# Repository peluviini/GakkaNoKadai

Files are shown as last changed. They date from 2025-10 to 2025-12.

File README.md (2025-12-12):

## GAS + Arduino kinda IOT Project
I'm making automatic controled fan that turns towards the hottest direction(assuming Human).

The fun's speeed is adjusted by caluculated Appearannce Temperature.

You can set some parameters in webpage, like targeted temperature, periodical notifications in discord.

> this is some practical assignment of my department 

### gas

Using clasp and so typescript

Gas is launching html

To deploy and see the page
> sh deploy.sh

### arduino
Trying to use esp-idf of rust

generate project->
> cargo generate esp-rs/esp-idf-template cargo

### memoranda
[GoogleSheet](https://docs.google.com/spreadsheets/d/12KPpMY7eV-cPQyw1QVUG0R_QObp-cpFYQhn_H8V2V_I/edit?gid=0#gid=0)

[See GAS codes](https://script.google.com/home/projects/1Yt5xZ93DhFCQdzscJVXwyot8o_8Z_F5k2Kss0VgZLZjdxhrT6P_gblSO/edit)

Page -> `sh deploy.sh` on gas directry

↓レポートのコピペ

<br>

# 1, 目的
### 電子デバイスを試行錯誤して作製する経験により,主体的に電子デバイス開発を行う能力をみにつける.

<br>

# 2, 原理・基礎的知見
## 2.1, 使用したセンサの概略と動作原理
## 2.1.1, 赤外線アレイセンサー
### 視野角60度の範囲を8×8ピクセルに分割して温度を取得する赤外線センサー.

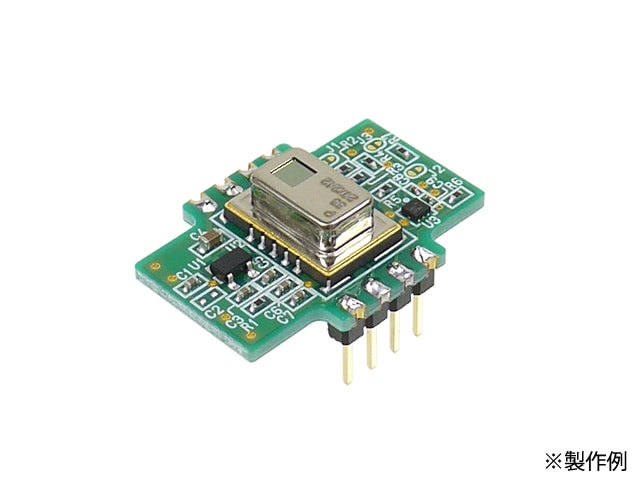
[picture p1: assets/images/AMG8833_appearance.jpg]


[AMG8833使用 赤外線アレイセンサー(Grid-EYE)モジュール](https://akizukidenshi.com/catalog/g/g116737/)

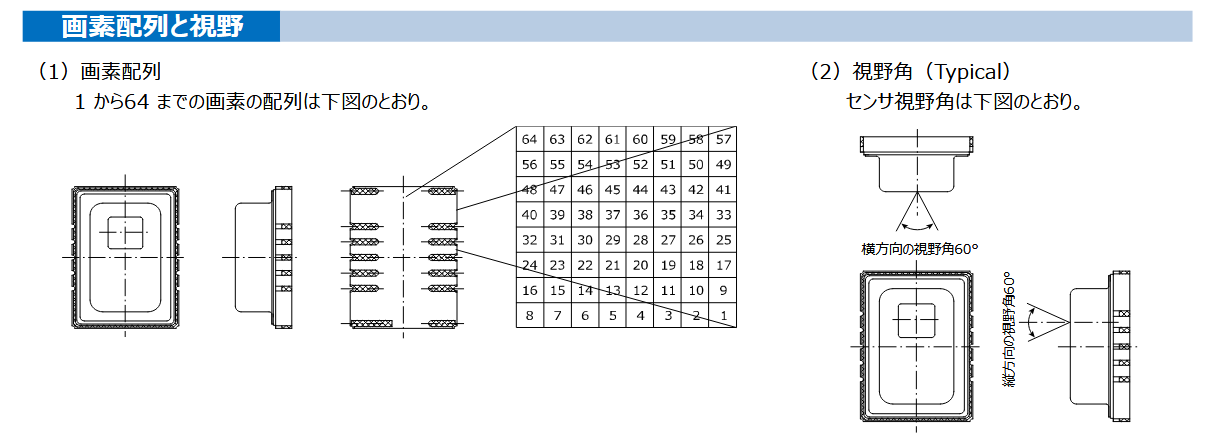
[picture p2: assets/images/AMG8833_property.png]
特性:画素配列と視野角


### 使用概略としては,値を縦方向に分割し方向ごとの合計値を計算,比較して熱の集まる方向として角度(ラジアン値)を判定する.

<br>

## 2.1.1, 温湿度センサー
### 温度及び湿度を取得するセンサー.

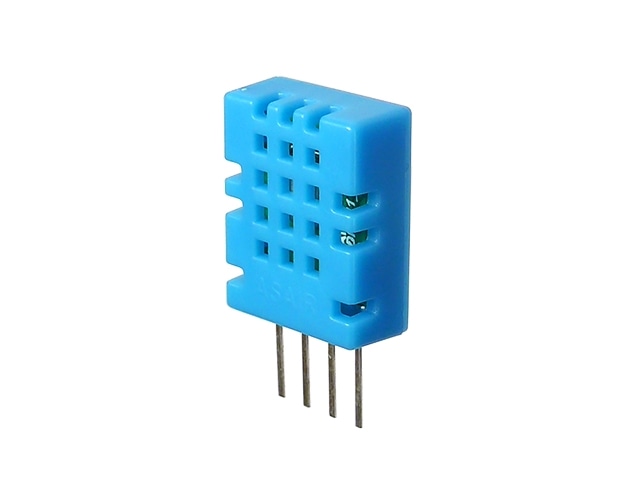
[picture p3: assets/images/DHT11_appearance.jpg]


[温湿度センサー モジュール DHT11](https://akizukidenshi.com/catalog/g/g107003/)

<br>

## 2.2, そのほか, 使用した特徴的な素子の概略と動作原理
## 2.2.1, USB PD シンクコントローラー
### type-c dip化モジュールと併せて使用し,PD規格とその給電する電力をコントロールするic. 今回のプロジェクトでは9[V]電源を得るために使用した.
[USB PD+BC シンクコントローラー CH224K](https://akizukidenshi.com/catalog/g/g118023/)

## 2.2.2, 三端子DCDCレギュレーター 5V
### 任意の電圧を5[V]に降圧する素子. esp-32などへの給電に使用.
[三端子DCDCレギュレーター 5V BP5293-50](https://akizukidenshi.com/catalog/g/g111188/)

<br>

# 3, 作品制作の実施概要
## 3.1, 作品名・キャッチコピー
### 作品名 「オートファ-トン」
### 全てが自律して動く卓上扇風機.

## 3.2, 制作の背景・目的
### デスクワークなどの作業では,常に同じ姿勢を保ち続けることは少なく,体の向きや位置は無意識のうちに変化する. 特に夏場,扇風機の風から体が外れてしまうもどかしさを経験した人は多いだろう. 従来の据え置き型扇風機は,一方向への送風や首振り機能によって一定範囲をカバーできるものの,それ以上の複雑な動きには対応できず,小回りが利かない.
### そこで今プロジェクトでは,使用者を自律的に追従し,常に適切な位置へ風を送り続け,さらに風量調節などの操作も自動化した卓上扇風機を開発する.

## 3.3, 想定ユーザーと利用シーン
### デスクワークをする人. 夏場ないし気温の高い日の屋内. その他, 対象が動く可能性があるが常に冷やし続けなければいけない状況.

## 3.4, 機能の概要
+ ### 人の体を検知/追尾し,風を常に当て続けてくれる
+ ### 温度と湿度,設定したターゲット体感温度から風量を自動で調節
### の2機能を備え,デバイス設定やリモコンとしての操作はすべてwebブラウザで行うことができる.
### また,部屋の温度をwebブラウザから確認することができる.

<br>

## 3.5, 構成要素と仕組み
## 3.5.1, 使用部品・物品
### 本体
+ ### ファン : Noctua NF-A20 5V PWM [商品ページ](https://www.google.com/url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)
+ ### モーター : FEETECHサーボ FT5325M [商品ページ](https://akizukidenshi.com/catalog/g/g116310/)
+ ### マイコン : ESP32-32D N4 [製品ページ](https://www.digikey.jp/ja/products/detail/espressif-systems/ESP32-WROOM-32D-N4/9381716)
+ ### 温湿度センサー モジュール DHT11　[商品ページ](https://akizukidenshi.com/catalog/g/g107003/)
+ ### USBtype-CコネクターDIP化キット [商品ページ](https://akizukidenshi.com/catalog/g/g115426/)
+ ### USB PD シンクコントローラー CH221K　[商品ページ](https://akizukidenshi.com/catalog/g/g118022/)
+ ### 三端子DCDCレギュレーター 5V BP5293-50 [商品ページ](https://akizukidenshi.com/catalog/g/g111188/)
+ ### LM2596 DC - DC降圧コンバータモジュール [商品ページ](https://www.amazon.co.jp/%E3%83%95%E3%83%AA%E3%83%BC%E3%83%95%E3%83%A9%E3%82%A4%E3%83%B3%E3%82%B0-6%E5%80%8B-LM2596-DC-DC%E9%99%8D%E5%9C%A7%E3%82%B3%E3%83%B3%E3%83%9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)
+ ### カーボン抵抗 [商品ページ(例として10[kΩ]1/4[W])](https://akizukidenshi.com/catalog/g/g125103/)
  (100, 510, 1k, 5.1k, 10k, 12k[Ω]のものを使用)
+ ### 電解コンデンサー10μF50V105℃ [商品ページ](https://akizukidenshi.com/catalog/g/g117897/)
+ ### NchパワーMOSFET 60V5A 2SK2796L [商品ページ](https://akizukidenshi.com/catalog/g/g107145/)
+ ### MOSFET 2N7000 [商品ページ](https://akizukidenshi.com/catalog/g/g109723/)
+ ### ガラスコンポジット・ユニバーサル基板 [商品ページ(例として両面Dタイプ)](https://akizukidenshi.com/catalog/g/g111960/)
+ ### ピンヘッダー [商品ページ](https://akizukidenshi.com/catalog/g/g100167/)
+ ### ピンソケット [商品ページ](https://akizukidenshi.com/catalog/g/g105779/)
+ ### プラネジ [商品ページ](https://akizukidenshi.com/catalog/g/g101861/)

### センサー機
+ ### AMG8833使用 赤外線アレイセンサー(Grid-EYE)モジュール [商品ページ](https://akizukidenshi.com/catalog/g/g116737/)
+ ### マイコン : ESP32-32D N4 [製品ページ](https://www.digikey.jp/ja/products/detail/espressif-systems/ESP32-WROOM-32D-N4/9381716)
+ ### ガラスコンポジット・ユニバーサル基板 [商品ページ(例として両面Dタイプ)](https://akizukidenshi.com/catalog/g/g111960/)
+ ### ピンヘッダー [商品ページ](https://akizukidenshi.com/catalog/g/g100167/)
+ ### ピンソケット [商品ページ](https://akizukidenshi.com/catalog/g/g105779/)

<br>

## 3.5.2, 回路図

## 本体の回路図
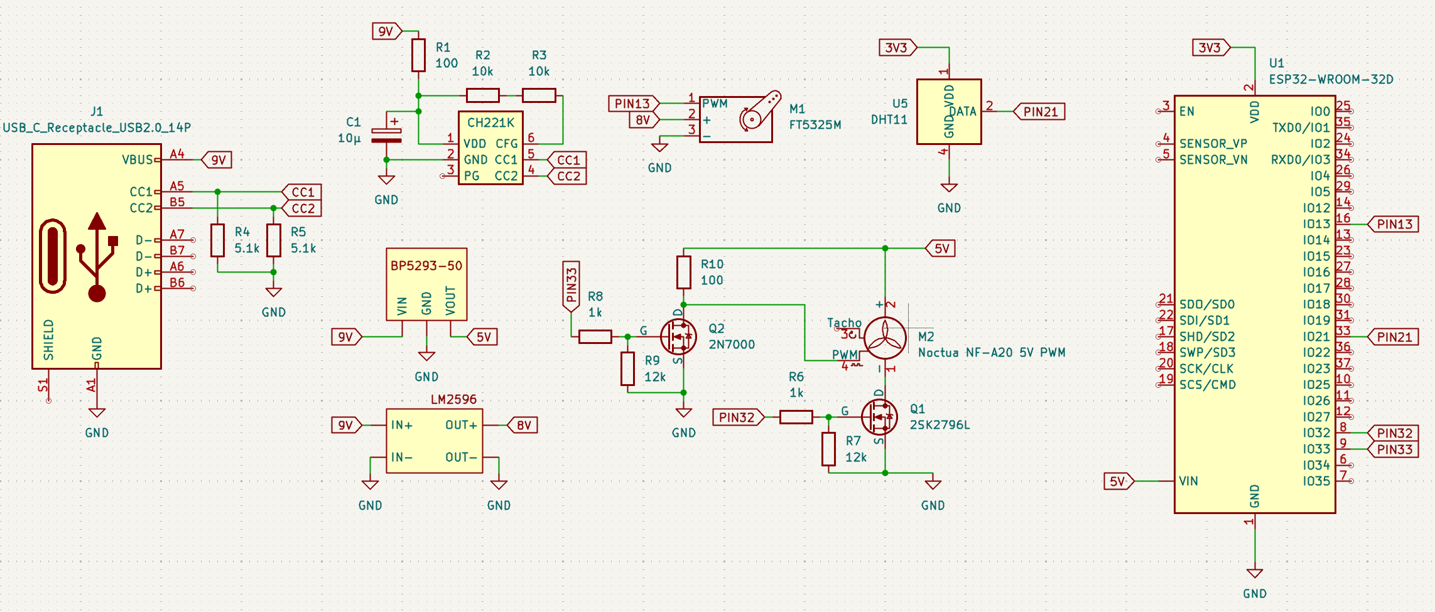
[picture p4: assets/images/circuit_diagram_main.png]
回路図:本体


## センサー機の回路図 / 実装した回路
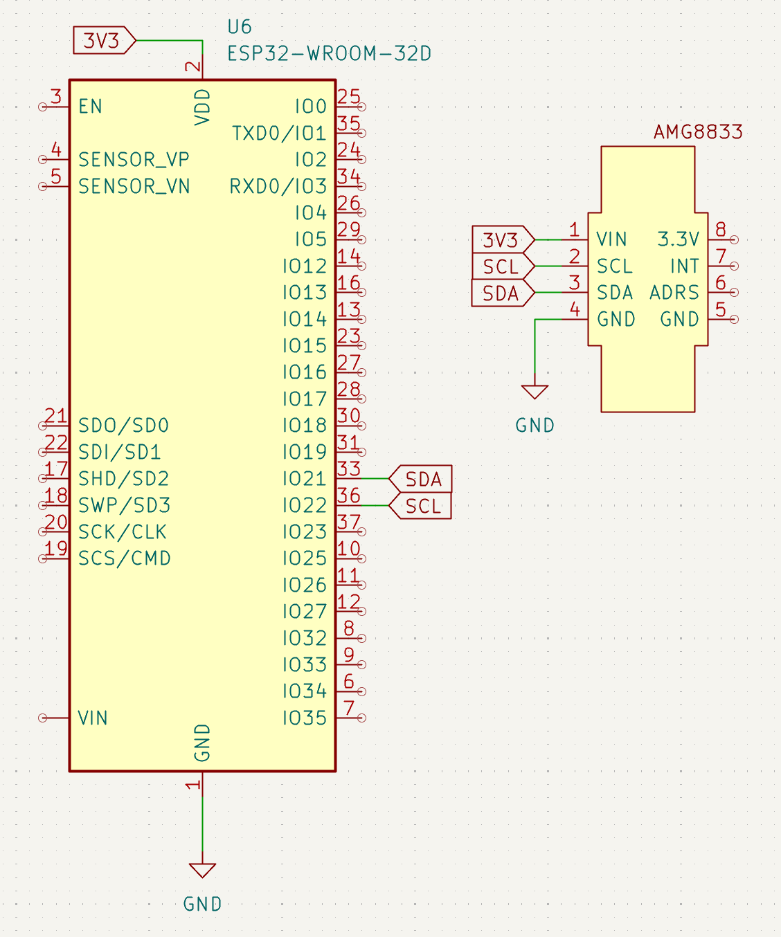
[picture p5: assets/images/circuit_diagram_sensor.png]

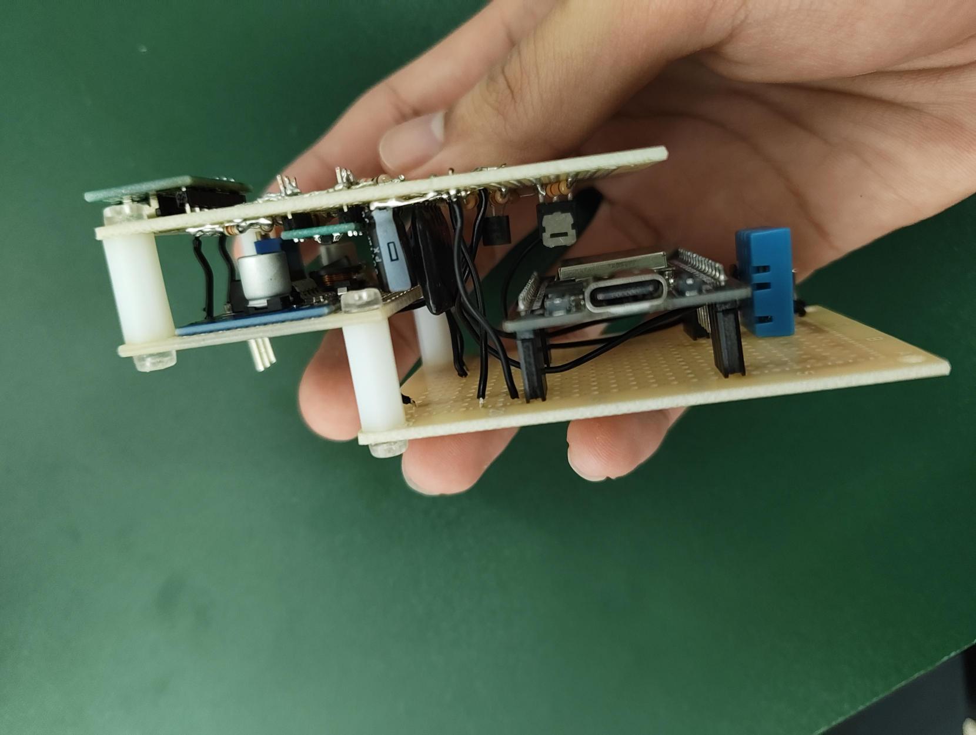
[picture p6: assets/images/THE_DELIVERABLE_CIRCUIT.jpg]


<br>

## 3.5.3, システム構成図
### システム構成図
```mermaid
flowchart BT

  subgraph Sensor Device
    a[起動]
    w[WiFiに接続]
    b[アレイセンサー値取得]
    c[値の分割 / 比較]
    d[角度の計算]
    e[GASにPostリクエスト]

    a ==> w
    w ==>|Error| a
    w ==>|Ok| b
    b ==> c
    c ==> d
    d ==> e
    e ==>|Ok| b
    e ==>|Error| a
  end

  subgraph Main Device
    A[起動]
    W[WiFiに接続]
    B[GASからのGet]
    C[DHT11の値取得]
    D[ユーザーが電源を]
    E[ファンの電源ON]
    F[サーボのpwm比への変換]
    G[風速の計算]
    G2[ファンのpwm比への変換]
    H[サーボへのpwm出力]
    I[ファンへのpwm出力]
    J[センサー値をGASにPost]
    K[ファンの電源OFF]

    A ==> W
    W ==>|Error| A
    W ==> |Ok| B
    B ==> |Error| A
    B ==> |Ok| C
    C ==> D
    D ==> |ON| E
    E ==> F
    F ==> G
    G ==> G2
    G2 ==> H
    H ==> I
    D ==>|OFF| K
    I ==> J
    J ==>|Ok| B
    J ==> |Error| A
    K ==> B
  end

```

<br>

## 3.6, 実際の動作例

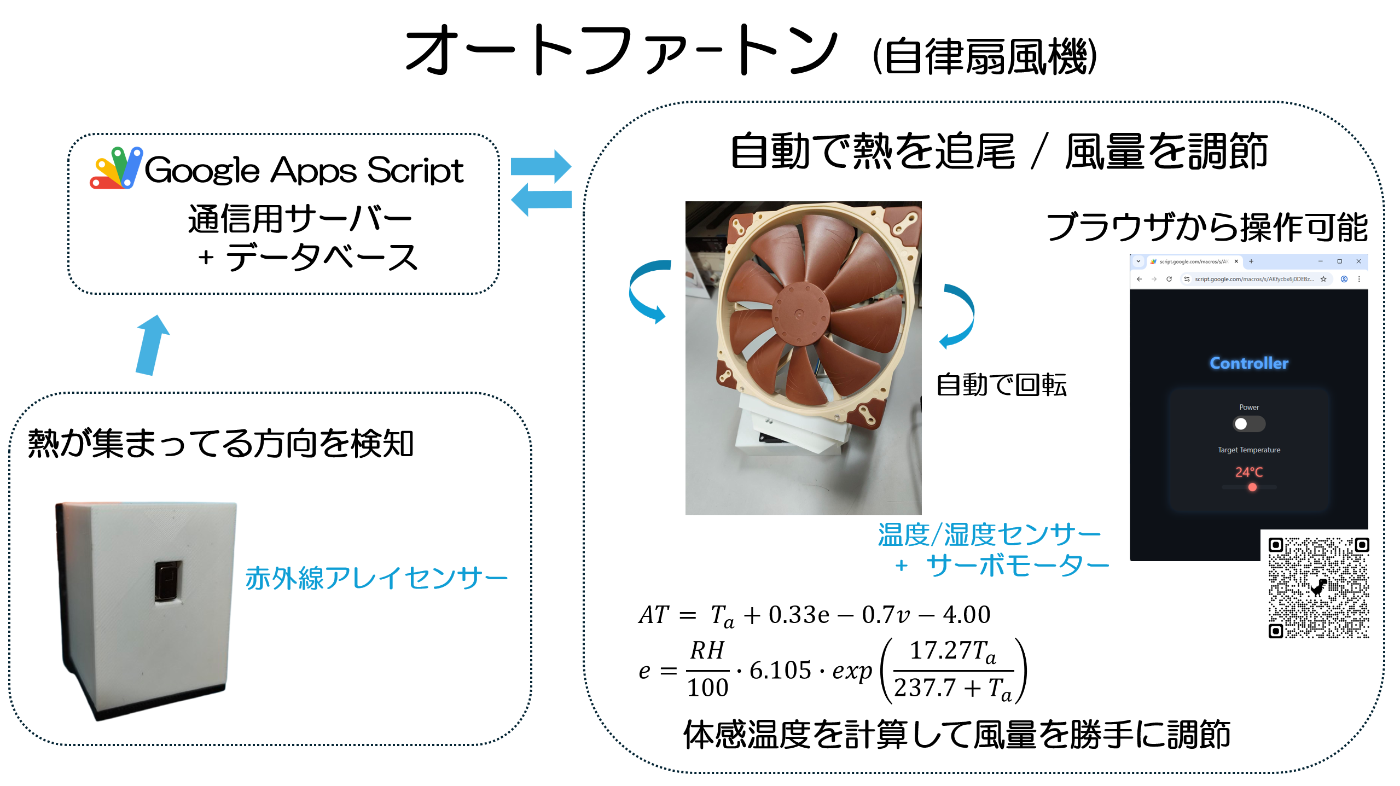
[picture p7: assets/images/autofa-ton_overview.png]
概略図


<br>

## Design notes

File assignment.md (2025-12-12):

# 1, 目的
### 電子デバイスを試行錯誤して作製する経験により,主体的に電子デバイス開発を行う能力をみにつける.

<br>

# 2, 原理・基礎的知見
## 2.1, 使用したセンサの概略と動作原理
## 2.1.1, 赤外線アレイセンサー
### 視野角60度の範囲を8×8ピクセルに分割して温度を取得する赤外線センサー.



図2.1, 赤外線アレイセンサー

[AMG8833使用 赤外線アレイセンサー(Grid-EYE)モジュール](https://akizukidenshi.com/catalog/g/g116737/)

特性:画素配列と視野角

図2.2, 赤外線アレイセンサーのセンサー取得値概要

### 使用概略としては,値を縦方向に分割し方向ごとの合計値を計算,比較して熱の集まる方向として角度(ラジアン値)を判定する.

<br>

## 2.1.1, 温湿度センサー
### 温度及び湿度を取得するセンサー.



図2.3, 温湿度センサー

[温湿度センサー モジュール DHT11](https://akizukidenshi.com/catalog/g/g107003/)

<br>

## 2.2, そのほか, 使用した特徴的な素子の概略と動作原理
## 2.2.1, USB PD シンクコントローラー
### type-c dip化モジュールと併せて使用し,PD規格とその給電する電力をコントロールするic. 今回のプロジェクトでは9[V]電源を得るために使用した.
[USB PD+BC シンクコントローラー CH224K](https://akizukidenshi.com/catalog/g/g118023/)

## 2.2.2, 三端子DCDCレギュレーター 5V
### 任意の電圧を5[V]に降圧する素子. esp-32などへの給電に使用.
[三端子DCDCレギュレーター 5V BP5293-50](https://akizukidenshi.com/catalog/g/g111188/)

<br>

# 3, 作品制作の実施概要
## 3.1, 作品名・キャッチコピー
### 作品名 「オートファ-トン」
### 全てが自律して動く卓上扇風機.

## 3.2, 制作の背景・目的
### デスクワークなどの作業では,常に同じ姿勢を保ち続けることは少なく,体の向きや位置は無意識のうちに変化する. 特に夏場,扇風機の風から体が外れてしまうもどかしさを経験した人は多いだろう. 従来の据え置き型扇風機は,一方向への送風や首振り機能によって一定範囲をカバーできるものの,それ以上の複雑な動きには対応できず,小回りが利かない.
### そこで今プロジェクトでは,使用者を自律的に追従し,常に適切な位置へ風を送り続け,さらに風量調節などの操作も自動化した卓上扇風機を開発する.

## 3.3, 想定ユーザーと利用シーン
### デスクワークをする人. 夏場ないし気温の高い日の屋内. その他, 対象が動く可能性があるが常に冷やし続けなければいけない状況.

## 3.4, 機能の概要
+ ### 人の体を検知/追尾し,風を常に当て続けてくれる
+ ### 温度と湿度,設定したターゲット体感温度から風量を自動で調節
### の2機能を備え,デバイス設定やリモコンとしての操作はすべてwebブラウザで行うことができる.
### また,部屋の温度をwebブラウザから確認することができる.

<br>

## 3.5, 構成要素と仕組み
## 3.5.1, 使用部品・物品
### 本体
+ ### ファン : Noctua NF-A20 5V PWM [商品ページ](https://www.google.com/url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)
+ ### モーター : FEETECHサーボ FT5325M [商品ページ](https://akizukidenshi.com/catalog/g/g116310/)
+ ### マイコン : ESP32-32D N4 [製品ページ](https://www.digikey.jp/ja/products/detail/espressif-systems/ESP32-WROOM-32D-N4/9381716)
+ ### 温湿度センサー モジュール DHT11　[商品ページ](https://akizukidenshi.com/catalog/g/g107003/)
+ ### USBtype-CコネクターDIP化キット [商品ページ](https://akizukidenshi.com/catalog/g/g115426/)
+ ### USB PD シンクコントローラー CH221K　[商品ページ](https://akizukidenshi.com/catalog/g/g118022/)
+ ### 三端子DCDCレギュレーター 5V BP5293-50 [商品ページ](https://akizukidenshi.com/catalog/g/g111188/)
+ ### LM2596 DC - DC降圧コンバータモジュール [商品ページ](https://www.amazon.co.jp/%E3%83%95%E3%83%AA%E3%83%BC%E3%83%95%E3%83%A9%E3%82%A4%E3%83%B3%E3%82%B0-6%E5%80%8B-LM2596-DC-DC%E9%99%8D%E5%9C%A7%E3%82%B3%E3%83%B3%E3%83%9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)
+ ### カーボン抵抗 [商品ページ(例として10[kΩ]1/4[W])](https://akizukidenshi.com/catalog/g/g125103/)
  (100, 510, 1k, 5.1k, 10k, 12k[Ω]のものを使用)
+ ### 電解コンデンサー10μF50V105℃ [商品ページ](https://akizukidenshi.com/catalog/g/g117897/)
+ ### NchパワーMOSFET 60V5A 2SK2796L [商品ページ](https://akizukidenshi.com/catalog/g/g107145/)
+ ### MOSFET 2N7000 [商品ページ](https://akizukidenshi.com/catalog/g/g109723/)
+ ### ガラスコンポジット・ユニバーサル基板 [商品ページ(例として両面Dタイプ)](https://akizukidenshi.com/catalog/g/g111960/)
+ ### ピンヘッダー [商品ページ](https://akizukidenshi.com/catalog/g/g100167/)
+ ### ピンソケット [商品ページ](https://akizukidenshi.com/catalog/g/g105779/)
+ ### プラネジ [商品ページ](https://akizukidenshi.com/catalog/g/g101861/)

### センサー機
+ ### AMG8833使用 赤外線アレイセンサー(Grid-EYE)モジュール [商品ページ](https://akizukidenshi.com/catalog/g/g116737/)
+ ### マイコン : ESP32-32D N4 [製品ページ](https://www.digikey.jp/ja/products/detail/espressif-systems/ESP32-WROOM-32D-N4/9381716)
+ ### ガラスコンポジット・ユニバーサル基板 [商品ページ(例として両面Dタイプ)](https://akizukidenshi.com/catalog/g/g111960/)
+ ### ピンヘッダー [商品ページ](https://akizukidenshi.com/catalog/g/g100167/)
+ ### ピンソケット [商品ページ](https://akizukidenshi.com/catalog/g/g105779/)

<br>

## 3.5.2, 回路図

## 本体の回路図
回路図:本体

図3.1, ファン側回路の回路図

## センサー機の回路図 / 実装した回路(本体)



図3.2, センサー機の回路図と実装後の本体回路

<br>

## 3.5.3, システム構成図
### システム構成図
```mermaid
flowchart BT

  subgraph Sensor Device
    a[起動]
    w[WiFiに接続]
    b[アレイセンサー値取得]
    c[値の分割 / 比較]
    d[角度の計算]
    e[GASにPostリクエスト]

    a ==> w
    w ==>|Error| a
    w ==>|Ok| b
    b ==> c
    c ==> d
    d ==> e
    e ==>|Ok| b
    e ==>|Error| a
  end

  subgraph Main Device
    A[起動]
    W[WiFiに接続]
    B[GASからのGet]
    C[DHT11の値取得]
    D[ユーザーが電源を]
    E[ファンの電源ON]
    F[サーボのpwm比への変換]
    G[風速の計算]
    G2[ファンのpwm比への変換]
    H[サーボへのpwm出力]
    I[ファンへのpwm出力]
    J[センサー値をGASにPost]
    K[ファンの電源OFF]

    A ==> W
    W ==>|Error| A
    W ==> |Ok| B
    B ==> |Error| A
    B ==> |Ok| C
    C ==> D
    D ==> |ON| E
    E ==> F
    F ==> G
    G ==> G2
    G2 ==> H
    H ==> I
    D ==>|OFF| K
    I ==> J
    J ==>|Ok| B
    J ==> |Error| A
    K ==> B
  end

```

図3.3, ワークフロー概要図

<br>

## 3.6, 実際の動作例

概略図

図3.4, デバイスの動作概略図

<br>

## 3.7, 工夫点・特徴
+ ### 回路の実装をできる限りコンパクトに収めた.
+ ### GASを通して,webアプリを作成した.
+ ### type-cを通す穴やサーボモーター,ファンを固定できる駆体の設計をした.
+ ### ファンの電源に対するスイッチ回路を組んだ.
+ ### モーター/ファン等の,電源に要求される電圧値が異なる物品を動かすために回路の電源部分とそこに降圧回路を二か所用意した. 一つについてはicを使用して降圧回路を組んだがこれは流れる電流が回路内のインダクタの定格を超えて発振したために失敗.

<br>

## 3.8, 今後の改良点・応用の可能性
## 3.8.1, 未達成の項目
### 1, 本体側プログラムのwifi処理(http通信のGet)がエラーを吐いており,http通信用に定義されたstructがエラーを持った状態で使いまわされるため二回目のGet通信でパニックを起こす.そのため,プログラム再起動分のラグ10秒前後がモーターの動作に生まれ,連続して動かない.
### 2, ファン部分のカバーを作り切れていない. またそのためファンの出力する風量の定義があいまいで,風速の計算が正確に定まっていない.
### 3, 体感温度の計算ロジックとファンの速度変更についてどちらも動作確認ができていない.

## 3.8.2, 改良点
+ ### 本体の駆体について,ファンや回路,駆体などを総じて軽量化/安価化し設置できる場所を壁などまで増やす.
+ ### webアプリから見ることができるデータを増やす(例: ファン本体の動作モデルなど).

## 3.8.2, 展望
+ ### 赤外線アレイセンサーについて,かなり高い精度で人のいる方向を検知することができた. この正確性をもつセンサーと熱の方向のロジックは扇風機に関係なく実装でき、色々な応用が利く可能性がある.
+ ### プログラムのデバッグをして,本体を想定通りに動かす.
+ ### 回路,駆体の再設計とデザイン性の考慮をし,さらにコンパクトにする.
+ ### ファンのカバーを風の通りなども考えて設計し,またプログラムの体感温度計算ロジック,回路のファンへの信号線増幅部分を見直してな直す. 
+ ### 場合によってはコンピュータ部分のスペックを上げ,カメラを用いた画像処理を行って精度を上げる.([これからの展望について](#4211-これからの展望について))
+ ### webアプリを改良し,UI/UXを改善する,実用的な機能を追加する.([アプリが使いづらいのでは](#4212-アプリが使いづらいのでは))

<br>

# 4, ユーザーレビュー
## ~~4.1, 文化祭での展示・意見募集の結果~~
貰えていないため割愛.

<br>

## 4.2, ピアレビュー結果
## 4.2.1, ピアレビューで寄せられた質問・コメント,それに対する回答
### 4.2.1.1, これからの展望について
### &ensp;回答: 場合によってはコンピュータ部分のスペックを上げ,カメラを用いた画像処理を行って精度を上げるかもしれないです.
### 4.2.1.2, アプリが使いづらいのでは
### &ensp;回答: 改良するつもりです.
### 4.2.1.3, 風速の調整の方法
### &ensp;回答: Australian Appearant Temperature Formulaというものを風速について解いて,プログラムに実装しています.<br>&ensp;ユーザーがアプリからターゲットの体感温度を設定したら風速が求まる仕組みです.
### 4.2.1.4, センサーを本体に取り付けてもいいのでは
### &ensp;回答: センサーの範囲の問題で扇風機と使用者が近くなければ有用でかつ色々な障壁が取り除かれるからありだと思う. ただセンサー部分の取り回しは悪くなる.

<br>

## 4.2.2, ピアレビューで行った質問・コメント,それに対する回答
### 4.2.2.1, 温度計の精度はどのくらい良いですか`4番に対して`
### &ensp;回答: 制度はかなり高いが,対象をぴったりくっつけないと反応しないという制約がある.
### 4.2.2.2, 通知等で使用者は目が覚めますか`8番に対して`
### &ensp;回答: データは,記録して寝ている時間等を解析するためのもので特にありません.
### &ensp;質問2: クッションのようにしたらいいのでは.
### 4.2.2.3, カーテンの開閉をできるようにしたらいいのでは`16番に対して`
### &ensp;回答: ありだと思う.

<br>

## 4.2.3, クラスメイトの作品を見て,今後の自分の制作に活かせるなと思った点
### 作品としては,デザインと第一印象がいかに大事かということを感じた.
### カメの水槽の水温を測っていたり,ノートPCの充電を自動化していたり,身の回りの物からシンプルだが面白いようなアイデアをたくさん見れて,何かを思いつくという上で,いい経験になったと思う.

<br>

## 4.3, 考察・レスポンス
### まだ動いていない部分を完成させて,制作物として完璧な状態にしたい.

<br>

# 5, 感想・考察
### 今回のプロジェクト/実習では,電子工作自体がほとんど初めてで分からない部分と格闘しながらであったが,部品や素子,センサーの選定,回路の設計,動作確認など一連の制作の流れを通して,アイデアをちょっとずつ形にして行けたことはとても面白かった.
### かなり楽しい経験であったし,新しいことに挑戦する機会にもなったのでこの経験をこれからに生かしていきたい.

<br>

# 7, 参考文献
(1) The Bureau of Meteorology. (5/2/2010). Thermal Comfort observations.[Government's Announcement]. [http://www.bom.gov.au/info/thermal_stress/#atapproximation](http://www.bom.gov.au/info/thermal_stress/#atapproximation)

<br>

# 8, 備考
+ [リポジトリ](https://github.com/peluviini/GakkaNoKadai)

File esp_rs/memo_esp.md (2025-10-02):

## To run

```
cargo run --release --bin fan
cargo run --release --bin sensor
```

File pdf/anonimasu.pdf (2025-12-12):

# 3 年 電気電子工学実験Ⅳ

# マイコンを用いた論理演算と実装

# 実施報告

2025 年 | 12 月 | 11 日

# 電子工学科 3 年 1 番 伊藤侑也

1, 目的

電子デバイスを試行錯誤して作製する経験により,主体的に電子デバイス開発を行う能力をみに つける.

## 2, 原理・基礎的知見

### 2.1, 使用したセンサの概略と動作原理

### 2.1.1, 赤外線アレイセンサー

視野角60度の範囲を8×8ピクセルに分割して温度を取得する赤外線センサー.


図2.1, 赤外線アレイセンサー

AMG8833使用 赤外線アレイセンサー(Grid-EYE)モジュール (https://akizukidenshi.com/catalog/g/g116737/)

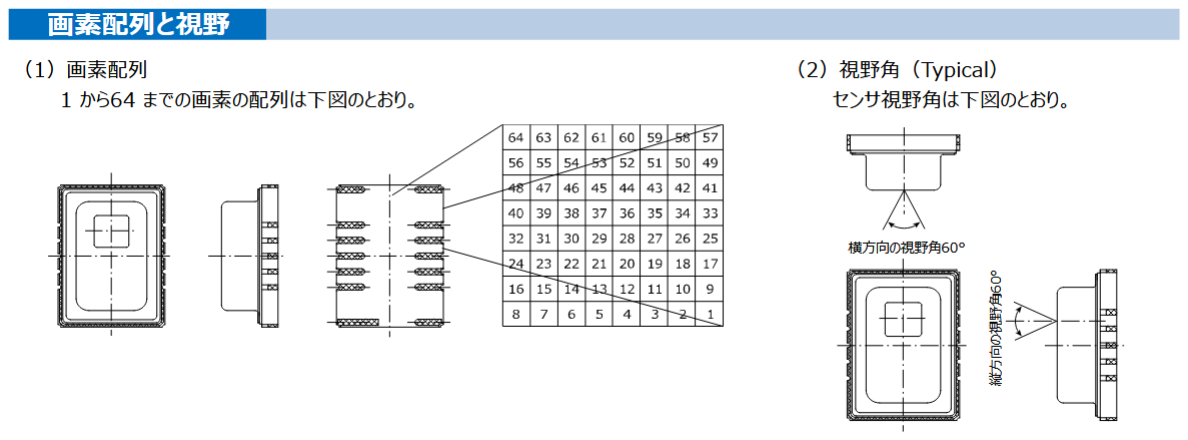
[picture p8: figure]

図2.2, 赤外線アレイセンサーのセンサー取得値概要

使用概略としては,値を縦方向に分割し方向ごとの合計値を計算,比較して熱の集まる方向とし て角度(ラジアン値)を判定する.

### 2.1.1, 温湿度センサー

温度及び湿度を取得するセンサー.


図2.3, 温湿度センサー

温湿度センサー モジュール DHT11 (https://akizukidenshi.com/catalog/g/g107003/)

### 2.2, そのほか, 使用した特徴的な素子の概略と動作原理

## 2.2.1, USB PD シンクコントローラー

type-c dip化モジュールと併せて使用し,PD規格とその給電する電力をコントロールするic. 今回 のプロジェクトでは9[V]電源を得るために使用した.

USB PD+BC シンクコントローラー CH224K (https://akizukidenshi.com/catalog/g/g118023/)

## 2.2.2, 三端子DCDCレギュレーター 5V

任意の電圧を5[V]に降圧する素子. esp-32などへの給電に使用.

三端子DCDCレギュレーター 5V BP5293-50 (https://akizukidenshi.com/catalog/g/g111188/)

## 3, 作品制作の実施概要

### 3.1, 作品名・キャッチコピー

作品名 「オートファ-トン」

全てが自律して動く卓上扇風機.

### 3.2, 制作の背景・目的

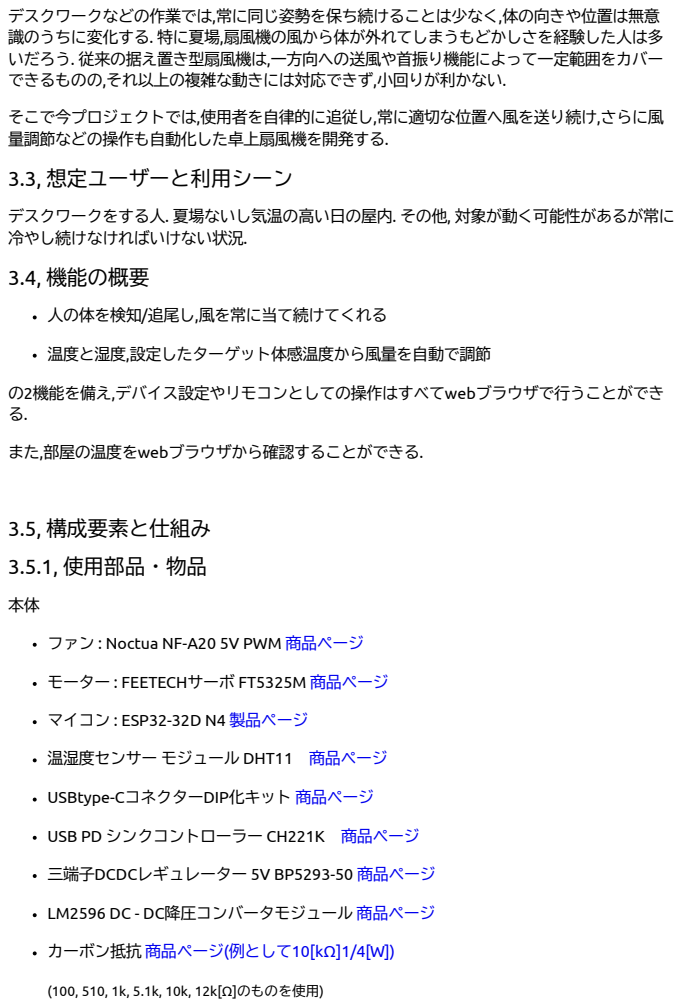
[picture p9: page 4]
温度と湿度,設定したターゲット体感温度から風量を自動で調節; の2機能を備え,デバイス設定やリモコンとしての操作はすべてwebブラウザで行うことができ る.; また,部屋の温度をwebブラウザから確認することができる.; 3.5, 構成要素と仕組み; 3.5.1, 使用部品・物品; マイコン : ESP32-32D N4 製品ページ; 三端子DCDCレギュレーター 5V BP5293-50 商品ページ; (100, 510, 1k, 5.1k, 10k, 12k[Ω]のものを使用)

デスクワークなどの作業では,常に同じ姿勢を保ち続けることは少なく,体の向きや位置は無意
識のうちに変化する. 特に夏場,扇風機の風から体が外れてしまうもどかしさを経験した人は多
いだろう. 従来の据え置き型扇風機は,一方向への送風や首振り機能によって一定範囲をカバー
できるものの,それ以上の複雑な動きには対応できず,小回りが利かない.

そこで今プロジェクトでは,使用者を自律的に追従し,常に適切な位置へ風を送り続け,さらに風
量調節などの操作も自動化した卓上扇風機を開発する.
3.3, 想定ユーザーと利用シーン

デスクワークをする人. 夏場ないし気温の高い日の屋内. その他, 対象が動く可能性があるが常に
冷やし続けなければいけない状況.
3.4, 機能の概要

人の体を検知/追尾し,風を常に当て続けてくれる

ファン : Noctua NF-A20 5V PWM 商品ページ (https://www.google.com/url?rct=j&opi=89978449)

モーター : FEETECHサーボ FT5325M 商品ページ (https://akizukidenshi.com/catalog/g/g116310/)

温湿度センサー モジュール DHT11 商品ページ (https://akizukidenshi.com/catalog/g/g107003/)

USBtype-CコネクターDIP化キット 商品ページ (https://akizukidenshi.com/catalog/g/g115426/)

USB PD シンクコントローラー CH221K 商品ページ (https://akizukidenshi.com/catalog/g/g118022/)

LM2596 DC - DC降圧コンバータモジュール 商品ページ (https://www.amazon.co.jp/%E3%83%95%E3%83%AA%E3%83%BC%E3%83%95%E3%83%A9%E3%82%A4%E3%83%B3%E3%82%B0-6%E5%80%8B-LM2596-DC-DC%E9%99%8D%E5%9C%A7%E3%82%B3%E3%83%B3%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)

カーボン抵抗 商品ページ(例として10[kΩ]1/4[W]) (https://akizukidenshi.com/catalog/g/g125103/)

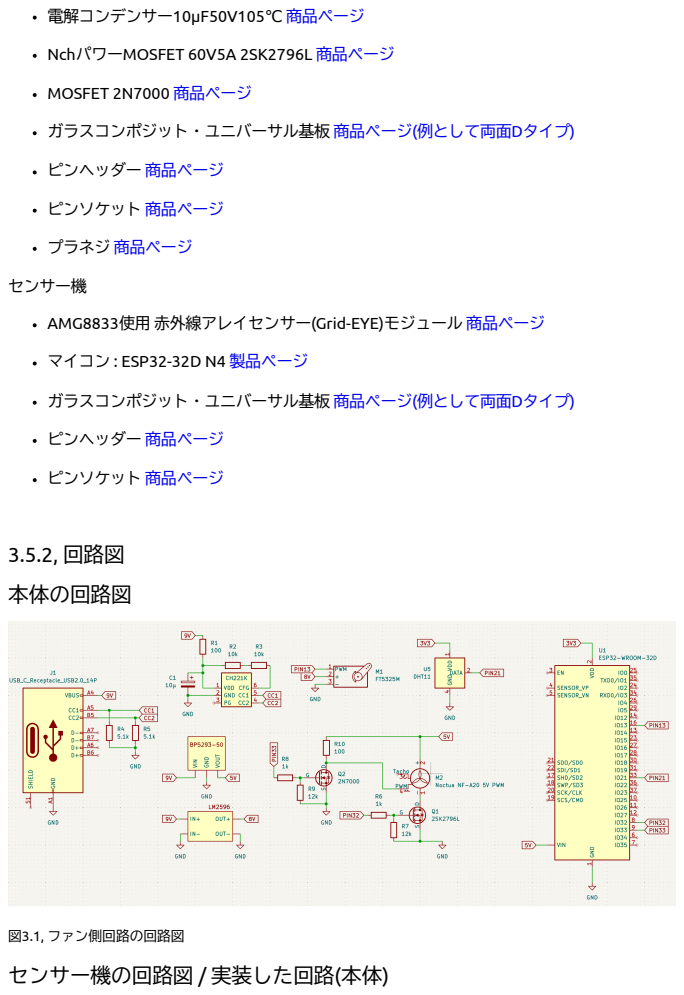
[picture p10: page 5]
電解コンデンサー10μF50V105℃ 商品ページ; NchパワーMOSFET 60V5A 2SK2796L 商品ページ; MOSFET 2N7000 商品ページ; ピンヘッダー 商品ページ; ピンソケット 商品ページ; プラネジ 商品ページ; センサー機; マイコン : ESP32-32D N4 製品ページ; 3.5.2, 回路図; 本体の回路図

ガラスコンポジット・ユニバーサル基板 商品ページ(例として両面Dタイプ) (https://akizukidenshi.com/catalog/g/g111960/)

AMG8833使用 赤外線アレイセンサー(Grid-EYE)モジュール 商品ページ (https://akizukidenshi.com/catalog/g/g116737/)

図3.1, ファン側回路の回路図
センサー機の回路図 / 実装した回路(本体)

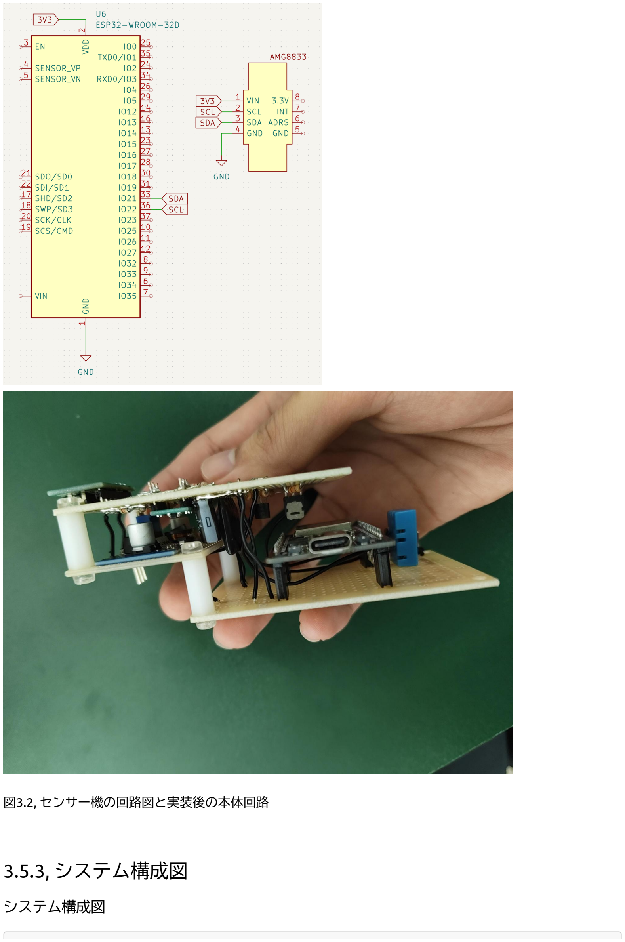
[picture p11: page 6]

図3.2, センサー機の回路図と実装後の本体回路

### 3.5.3, システム構成図

システム構成図

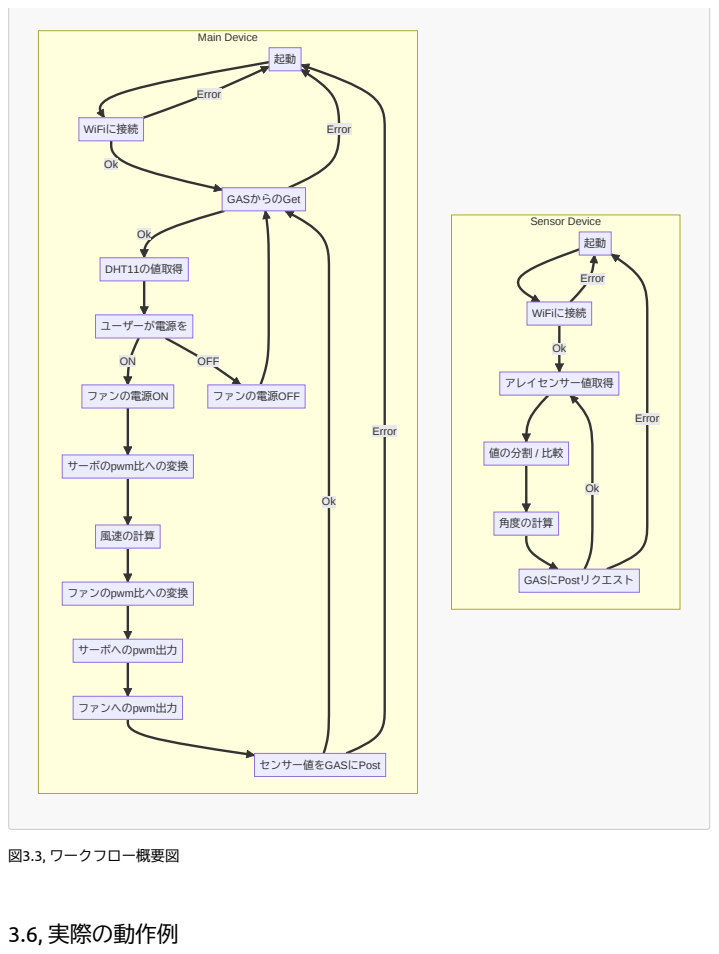
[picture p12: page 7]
Main Device; Error; OFF; WiFiに接続; GASからのGet; DHT11の値取得; ユーザーが電源を; ファンの電源ON; サーボのpwm比への変換; 風速の計算; ファンのpwm比への変換; サーボへのpwm出力; ファンへのpwm出力; ファンの電源OFF; センサー値をGASにPost; Sensor Device; アレイセンサー値取得; 値の分割 / 比較; 角度の計算; GASにPostリクエスト; 図3.3, ワークフロー概要図; 3.6, 実際の動作例


図3.4, デバイスの動作概略図

### 3.7, 工夫点・特徴

回路の実装をできる限りコンパクトに収めた.

GASを通して,webアプリを作成した.

type-cを通す穴やサーボモーター,ファンを固定できる駆体の設計をした.

ファンの電源に対するスイッチ回路を組んだ.

モーター/ファン等の,電源に要求される電圧値が異なる物品を動かすために回路の電源部 分とそこに降圧回路を二か所用意した. 一つについてはicを使用して降圧回路を組んだが これは流れる電流が回路内のインダクタの定格を超えて発振したために失敗.

### 3.8, 今後の改良点・応用の可能性

## 3.8.1, 未達成の項目

1, 本体側プログラムのwifi処理(http通信のGet)がエラーを吐いており,http通信用に定義された structがエラーを持った状態で使いまわされるため二回目のGet通信でパニックを起こす.その ため,プログラム再起動分のラグ10秒前後がモーターの動作に生まれ,連続して動かない.

2, ファン部分のカバーを作り切れていない. またそのためファンの出力する風量の定義があい まいで,風速の計算が正確に定まっていない.

3, 体感温度の計算ロジックとファンの速度変更についてどちらも動作確認ができていない.

## 3.8.2, 改良点

本体の駆体について,ファンや回路,駆体などを総じて軽量化/安価化し設置できる場所を壁 などまで増やす.

webアプリから見ることができるデータを増やす(例: ファン本体の動作モデルなど).
3.8.2, 展望

赤外線アレイセンサーについて,かなり高い精度で人のいる方向を検知することができた. この正確性をもつセンサーと熱の方向のロジックは扇風機に関係なく実装でき、色々な応 用が利く可能性がある.

プログラムのデバッグをして,本体を想定通りに動かす.

回路,駆体の再設計とデザイン性の考慮をし,さらにコンパクトにする.

ファンのカバーを風の通りなども考えて設計し,またプログラムの体感温度計算ロジック, 回路のファンへの信号線増幅部分を見直してな直す.

場合によってはコンピュータ部分のスペックを上げ,カメラを用いた画像処理を行って精 度を上げる.(これからの展望について)

webアプリを改良し,UI/UXを改善する,実用的な機能を追加する.(アプリが使いづらいので は)

## 4, ユーザーレビュー

### 4.1, 文化祭での展示・意見募集の結果

貰えていないため割愛.

### 4.2, ピアレビュー結果

### 4.2.1, ピアレビューで寄せられた質問・コメント,それに対する回答

4.2.1.1, これからの展望について

回答: 場合によってはコンピュータ部分のスペックを上げ,カメラを用いた画像処理を行って精 度を上げるかもしれないです.

4.2.1.2, アプリが使いづらいのでは

回答: 改良するつもりです.

4.2.1.3, 風速の調整の方法

回答: Australian Appearant Temperature Formulaというものを風速について解いて,プログラ ムに実装しています.
ユーザーがアプリからターゲットの体感温度を設定したら風速が求まる仕組みです.

4.2.1.4, センサーを本体に取り付けてもいいのでは

回答: センサーの範囲の問題で扇風機と使用者が近くなければ有用でかつ色々な障壁が取り除 かれるからありだと思う. ただセンサー部分の取り回しは悪くなる.

### 4.2.2, ピアレビューで行った質問・コメント,それに対する回答

4.2.2.1, 温度計の精度はどのくらい良いですか4番に対して

回答: 制度はかなり高いが,対象をぴったりくっつけないと反応しないという制約がある.

4.2.2.2, 通知等で使用者は目が覚めますか8番に対して

回答: データは,記録して寝ている時間等を解析するためのもので特にありません.

質問2: クッションのようにしたらいいのでは.

4.2.2.3, カーテンの開閉をできるようにしたらいいのでは16番に対して

回答: ありだと思う.

### 4.2.3, クラスメイトの作品を見て,今後の自分の制作に活かせるなと思っ

た点

作品としては,デザインと第一印象がいかに大事かということを感じた.

カメの水槽の水温を測っていたり,ノートPCの充電を自動化していたり,身の回りの物からシン プルだが面白いようなアイデアをたくさん見れて,何かを思いつくという上で,いい経験になっ たと思う.

### 4.3, 考察・レスポンス

まだ動いていない部分を完成させて,制作物として完璧な状態にしたい.

## 5, 感想・考察

今回のプロジェクト/実習では,電子工作自体がほとんど初めてで分からない部分と格闘しなが らであったが,部品や素子,センサーの選定,回路の設計,動作確認など一連の制作の流れを通して, アイデアをちょっとずつ形にして行けたことはとても面白かった.

かなり楽しい経験であったし,新しいことに挑戦する機会にもなったのでこの経験をこれからに 生かしていきたい.

## 7, 参考文献

(1) The Bureau of Meteorology. (5/2/2010). Thermal Comfort observations.[Government's Announcement]. http://www.bom.gov.au/info/thermal_stress/#atapproximation

8, 備考

リポジトリ (https://github.com/peluviini/GakkaNoKadai)

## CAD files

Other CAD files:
assets/models/temp_gakka_sensor_case.blend

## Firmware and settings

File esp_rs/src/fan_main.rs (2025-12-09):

use anyhow::{Ok, Result};
use esp_idf_hal::gpio::PinDriver;
use esp_idf_hal::peripherals::Peripherals;
use esp_idf_hal::{
    delay::{self}, gpio::IOPin, /*i2c::{I2cConfig, I2cDriver},*/ ledc::{
        config::TimerConfig, LedcDriver, LedcTimerDriver
    }, units::Hertz
};
//use esp_idf_hal::prelude::*;
use std::time::Duration;
use dht11::Dht11;
//use bme280::i2c::BME280;

use serde::{Deserialize, Serialize};

use core::convert::TryInto;

use embedded_svc::{
    http::{client::Client as HttpClient, Method},
    utils::io,
    io::Write,
    wifi::{AuthMethod, ClientConfiguration},
};

use esp_idf_svc::http::client::EspHttpConnection;
use esp_idf_svc::wifi::{BlockingWifi, EspWifi};
use esp_idf_svc::{eventloop::EspSystemEventLoop, nvs::EspDefaultNvsPartition};

use log::{error, info};

use core::f32::consts::{PI, E};

use serde_json::json;
use std::time::{SystemTime, UNIX_EPOCH};

#[derive(Debug, Serialize, Deserialize, Clone, PartialEq)]
#[serde(rename_all = "UPPERCASE")]
enum Power {
    On,
    Off,
}

#[derive(Debug, Serialize, Deserialize, Clone, Default)]
struct ParamsSent {
    power: Power,
    #[serde(rename = "targetTemp")]
    target_temp: u32,
    angle: f32,
}
impl Default for Power {
    fn default() -> Self {
        Power::Off
    }
}

const URL_GAS_RECIVE: &'static str = "https://script.google.com/macros/s/AKfycbyzJ4FzcEer9bqgk3ezTEBg1AbRXzql5Z2MJARKLkfHw48nOaOzjNBcAhAJzpFwbsGyZg/exec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";
const URL_GAS: &'static str = "https://script.google.com/macros/s/AKfycbyzJ4FzcEer9bqgk3ezTEBg1AbRXzql5Z2MJARKLkfHw48nOaOzjNBcAhAJzpFwbsGyZg/exec";

const SSID: &'static str = "pelu's Nothing Phone";
const PASSWORD: &'static str = "kws8b8tj";

fn main() -> Result<()> {
    esp_idf_svc::sys::link_patches();
    use std::result::Result::Ok;
    match run() {
        Ok(_) => Ok(()),
        Err(_) => {
            std::thread::sleep(Duration::from_secs(5));
            
            unsafe { esp_idf_sys::esp_restart(); }
        },
    }
}

fn run() -> Result<()> {

    let peripherals = Peripherals::take().unwrap();
    let sys_loop = EspSystemEventLoop::take()?;
    let nvs = EspDefaultNvsPartition::take()?;
    let mut wifi = BlockingWifi::wrap(
    EspWifi::new(peripherals.modem, sys_loop.clone(), Some(nvs))?,
    sys_loop,
    )?;

    use esp_idf_svc::http::client::Configuration;
    connect_wifi(&mut wifi)?;
    let mut client = HttpClient::wrap(EspHttpConnection::new(
        &Configuration {
            use_global_ca_store: true,
            crt_bundle_attach: Some(esp_idf_sys::esp_crt_bundle_attach),
            buffer_size_tx: Some(4096),
            ..Default::default()
        }
    )?);

    let timer_fan = LedcTimerDriver::new(
        peripherals.ledc.timer0,
        &TimerConfig::default()
            .frequency(Hertz(25 * 1000).into())
            .resolution(esp_idf_hal::ledc::Resolution::Bits8),
    )?;
    let timer_servo = LedcTimerDriver::new(
        peripherals.ledc.timer1,
        &TimerConfig::default()
            .frequency(Hertz(50).into())
            .resolution(esp_idf_hal::ledc::Resolution::Bits16),
    )?;

    let mut fan_vin = PinDriver::output(peripherals.pins.gpio32)?;
    let mut servo_vin = PinDriver::output(peripherals.pins.gpio12)?;
    let mut pwm_fan = LedcDriver::new(
        peripherals.ledc.channel0,
        &timer_fan,
        peripherals.pins.gpio33,
    )?;
    let mut pwm_servo = LedcDriver::new(
        peripherals.ledc.channel1,
        &timer_servo,
        peripherals.pins.gpio13,
    )?;

    let max_duty_fan = pwm_fan.get_max_duty();
    let max_duty_servo = pwm_servo.get_max_duty();

    let period_us = 20_000f32;

    //let duty_min = (max_duty_servo as f32 * (500.0 / period_us)) as u32;
    let duty_mid = (max_duty_servo as f32 * (1500.0 / period_us)) as u32;
    //let duty_max = (max_duty_servo as f32 * (2500.0 / period_us)) as u32;
    
    
    let dht_pin = PinDriver::input_output_od(peripherals.pins.gpio21.downgrade()).unwrap();
    let mut dht = Dht11::new(dht_pin);
    let mut delay = delay::Ets;
    /*let sda = peripherals.pins.gpio22;
    let scl = peripherals.pins.gpio21;
    let config = I2cConfig::new()
        .baudrate(100.kHz().into())
        .sda_enable_pullup(true)
        .scl_enable_pullup(true);
    let i2c = I2cDriver::new(peripherals.i2c0, sda, scl, &config)?;

    let mut bmp280 = BME280::new_primary(i2c);
    let mut delay = delay::Ets;
    bmp280.init(&mut delay).unwrap();*/

    

    let mut datas: ParamsSent = Default::default();

    loop {

        let mut temperature = 0.;
        let mut humidity = 0.;
        //let dht_data = dht.perform_measurement(&mut delay).unwrap();
        match dht.perform_measurement(&mut delay) {
            Ok(m) => {
                
                println!(
                    "temp: {}C, humidity: {}%",
                    (m.temperature as f32 / 10.0),
                    (m.humidity as f32 / 10.0)
                );
                temperature = m.temperature as f32 / 10.;
                humidity = m.humidity as f32 / 10.;
            }
            Err(e) => println!("{:?}", e),
        }
        /*let bmp = bmp280.measure(&mut delay).unwrap();
         println!(
            "Relative Humidity = {:3.2} %,   Temperature = {:3.2} °C,   Pressure = {:4.2} hPa",
            bmp.humidity,
            bmp.temperature,
            bmp.pressure / 100_f32
        );*/

        use std::result::Result::Ok;
        match get(/*&mut client*/) {
            Ok(d) => {
                println!("ok");
                datas = d.clone();
                println!("{:?} : {:?} : {:?}", datas.power, datas.target_temp, datas.angle);
            }
            Err(e) => {
                println!("err: {:?}", e);
            }
        }

        if datas.power == Power::On {
            fan_vin.set_high()?;
            servo_vin.set_high()?;

            let duty_servo = (max_duty_servo as f32 * ((1500. + (datas.angle / (PI / 2.) * 1000.)) / period_us)) as u32;
            
            let wind_speed = {
                            //let temperature = dht_data.temperature as f32;
                            //let humidity = dht_data.humidity as f32;
                            let e = (humidity / 100.0) * 6.105 * E.powf((17.27 * temperature) / (237.7 + temperature));
                            let v = (temperature + 0.33 * e - (datas.target_temp as f32) - 4.0) / 0.7;
                            v.max(0.0)
                        };
            println!("wind: {}", wind_speed);
            let duty_fan = {
                let q_max = 146.9;
                let v_max = q_max;

                let max = max_duty_fan as f32;
                let ratio = wind_speed / v_max;
                let mut duty = max * ratio;
                if duty > max {
                    duty = max;
                } else if duty < max * 0.2 {
                    duty = max * 0.2;
                }

                duty
            };

            println!("pwm servo: {}", duty_servo);
            pwm_servo.set_duty(duty_servo)?;
            println!("pwm fan: {}", duty_fan);
            pwm_fan.set_duty(duty_fan as u32)?;
            
            post(/*&mut client,*/ temperature as f32, humidity as f32, wind_speed).unwrap();

        } else {

            pwm_servo.set_duty(duty_mid)?;
            fan_vin.set_low()?;
            servo_vin.set_low()?;
        }

        std::thread::sleep(Duration::from_millis(50));
    }

}

fn connect_wifi(wifi: &mut BlockingWifi<EspWifi<'static>>) -> anyhow::Result<()> {
    use embedded_svc::wifi::Configuration;
    let wifi_configuration: Configuration = Configuration::Client(ClientConfiguration {
        ssid: SSID.try_into().unwrap(),
        bssid: None,
        auth_method: AuthMethod::WPA2Personal,
        password: PASSWORD.try_into().unwrap(),
        channel: None,
        ..Default::default()
    });

    wifi.set_configuration(&wifi_configuration)?;

    wifi.start()?;
    info!("Wifi started");

    wifi.connect()?;
    info!("Wifi connected");

    wifi.wait_netif_up()?;
    info!("Wifi netif up");

    Ok(())
}
fn get(/*client: &mut HttpClient<EspHttpConnection>*/) -> anyhow::Result<ParamsSent> {

    use esp_idf_svc::http::client::Configuration;
    let mut client = HttpClient::wrap(EspHttpConnection::new(
        &Configuration {
            use_global_ca_store: true,
            crt_bundle_attach: Some(esp_idf_sys::esp_crt_bundle_attach),
            buffer_size_tx: Some(4096),
            ..Default::default()
        }
    )?);

    println!("get");
    let headers = [("accept", "application/json"), ("connection", "close")];

    let request = client.request(Method::Get, URL_GAS_RECIVE, &headers)?;
    info!("-> GET {URL_GAS_RECIVE}");
    let mut response = request.submit()?;

    let status = response.status();
    info!("<- {status}");
    let mut buf = [0u8; 1024];
    let bytes_read = io::try_read_full(&mut response, &mut buf).map_err(|e| e.0)?;
    info!("Read {bytes_read} bytes");
    use std::result::Result::Ok;
    match std::str::from_utf8(&buf[0..bytes_read]) {
        Ok(body_string) => info!(
            "Response body (truncated to {} bytes): {:?}",
            buf.len(),
            body_string
        ),
        Err(e) => error!("Error decoding response body: {e}"),
    };

    if let Ok(body_str) = std::str::from_utf8(&buf[..bytes_read]) {
        info!("Body ({} bytes): {}", bytes_read, body_str);
    } else {
        error!("Body is not valid UTF-8");
    }

    let value: serde_json::Value = serde_json::from_slice(&buf[..bytes_read])?;

    //println!("value: {:?}", value);

    let params = serde_json::from_value(value)?;

    println!("get end");
    Ok(params)
}


fn post(
    /*client: &mut HttpClient<EspHttpConnection>,*/
    temperature: f32,
    humidity: f32,
    wind_speed: f32,
) -> anyhow::Result<()> {

    use esp_idf_svc::http::client::Configuration;
    let mut client = HttpClient::wrap(EspHttpConnection::new(
        &Configuration {
            use_global_ca_store: true,
            crt_bundle_attach: Some(esp_idf_sys::esp_crt_bundle_attach),
            buffer_size_tx: Some(4096),
            ..Default::default()
        }
    )?);

    let _ = SystemTime::now().duration_since(UNIX_EPOCH)
        .map(|d: Duration| d.as_secs())
        .unwrap_or(0);
    let json = json!({
        "method": "post",
        "content": "fan",
        "params": {
            "temperature": temperature,
            "humidity": humidity,
            "wind_speed": wind_speed,
        }
    });
    let payload = &serde_json::to_vec(&json).unwrap();

    let content_length_header = format!("{}", payload.len());
    let headers = [
        ("content-type", "application/json"),
        ("content-length", &*content_length_header),
    ];

    let mut request = client.post(URL_GAS, &headers)?;
    request.write_all(payload)?;
    request.flush()?;
    info!("-> POST {}", URL_GAS);
    
    let mut response = request.submit()?;
    let status = response.status();
    info!("<- status: {}", status);

    let mut body_vec: Vec<u8> = Vec::new();
    let mut tmp = [0u8; 512];
    loop {
        let n = response.read(&mut tmp)?;
        if n == 0 {
            break;
        }
        body_vec.extend_from_slice(&tmp[..n]);
    }

    use std::result::Result::Ok;
    match std::str::from_utf8(&body_vec) {
        Ok(body_string) => info!("Response body: {}", body_string),
        Err(e) => error!("Error decoding response body: {}", e),
    };

    Ok(())
}

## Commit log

2025-09-22 Add: testing servo and fan
2025-10-05 Fix: sensor's post, gas setting
    [fan_main.rs, sensor_main.rs]
2025-10-15 Fix: it might run completely, I believe :(
    [fan_main.rs, sensor_main.rs]
2025-12-10 Add: Ganbatta Kadai
    [temp_gakka_sensor_case.blend]
2025-12-12 Add: Kicad project and its directory
    [denshi_kadai_3D_IoT.kicad_pcb, denshi_kadai_3D_IoT.kicad_sch]
